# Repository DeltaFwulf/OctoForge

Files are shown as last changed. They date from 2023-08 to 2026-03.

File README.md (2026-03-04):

# OctoForge: 
A work in progress electric furnace capable of reaching chamber temperatures of 1200 C.

This project is simply a display of technical knowledge and something through which we have learned further technologies. The hope is that any projects tackled in the future will be easier due to the experience and skills learned here.

There are three main areas of which the furnace is comprised:
- Mechanical - Frame design complete and in production, insulation under final design iteration, heating element under final design iteration.
- Power electronics - Still iterating over design and testing.
- Control electronics - Yet to be started.

Progress is being tracked [here](https://github.com/users/DeltaFwulf/projects/2).

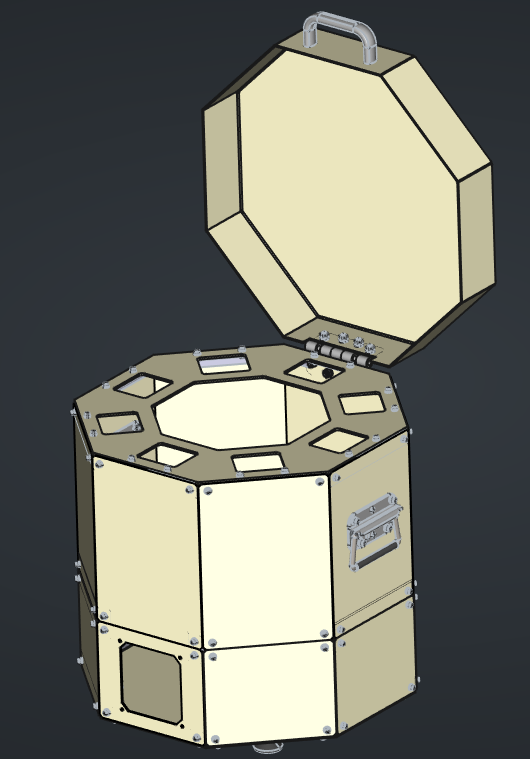
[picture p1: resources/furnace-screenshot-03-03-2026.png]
Screenshot of OctoForge


## How to use this project?
The following software is required to view the various CAD files:
- FreeCAD-1.0.2
- KiCAD-9.0

## How to reproduce OctoForge?
- Sheet metal components were ordered from [Fractory](https://fractory.com/) with the following parameters:
  - Thicknesses:
    - Plates: 3mm
    - Lower panels: 2mm
    - Upper panels: 1.5mm
    - Lid: 2mm
  - High temperature components will be black oxide treated, and exterior components will be painted with high temperature paint and clear coat.
- The other mechanical components were machined from stock using the drawings provided within the CAD directory.
- Fittings were ordered using the provided [BOM](Documentation/Mechanical/BOM.ods) from [Accu](https://www.accu.co.uk/) and [Vital Parts](https://www.vital-parts.co.uk/).
- Feet and handles are standard components, but were sourced from WDS components as listed in the BOM.
- PCBs were ordered from [JLCPCB](jlcpcb.com) with the following parameters:
  - 2 layers
  - PCB thickness - 1.6mm
  - Material type - TG135
  - Outer copper weight - 1oz

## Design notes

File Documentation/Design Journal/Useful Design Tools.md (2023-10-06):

## Product Design Specification

This document outlines the requirements that the design must fulfil, as well as how these requirements were chosen and their priority. This is a very useful tool for constraining the design early on, reducing feature creep and confusion as to where to begin.

## Morphological Charts

This is a graphical method for choosing how to solve different requirements in the PDS. We create a table where the y-axis is requirements and the x-axis consists of concepts of how to solve each requirement. A path is chosen through the table by evaluating the pros and cons of each sub-design concept, allowing a rough image of the overall system to form quickly. Changes can of course be made later on, but this is quite an efficient way to think outside of the one or two examples you thought of on the spot before starting, when a better third option may exist. (brainstorming really helps here)

## Product Breakdown System

This is a super useful way to organise large assemblies. Every component, assembly, and subassembly is assigned a number. This allows easy organisation of parts in spreadsheets containing specific data and CAD structuring through subassemblies. There's a lot more that can be done, such as quantifying progress within a project by assigning weights to not only parts but tasks, and their corresponding progresses.

A good explanation was actually done on Wintergatan's video [here](https://www.youtube.com/watch?v=zVyEsMiwvVc)

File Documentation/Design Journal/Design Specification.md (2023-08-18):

## Product Specification

- Efficient enough to melt copper
- PID control using homemade electronics
- uses standardised components
- relatively portable without causing damage to any party including furnace
- fails safe pls
- easily maintained
- safe power supply: overcurrent protection, requires earthing, hard to shock self on, reasonable safety factor, adequate cooling

## V1 issues
- too easy to touch mains voltage
- hard to control
- ludicrous inefficiency leading to poor performance and high maintenance costs
- difficult to repair
- difficult to manufacture
- choppy voltage source may have led to excessive coil wear
- poor analytical understanding

## Useful links

### References

### Shopping list

## Hardware used

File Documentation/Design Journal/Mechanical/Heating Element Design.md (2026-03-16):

![[heating element model.png]]
*Heating element model*
## Element Geometry
---
Given a maximum power requirement, heating element count, and selected material, the heating element geometry may be defined, and stock sourced.

The general design of a single heating element is that of a coiled wire, bent into a circular loop that sits within a channel on the chamber's inner wall. This element will provide power via radiation into the chamber.

![[steady power vs rockwool thickness, 1200C.png]] 
*Required thermal power required vs rockwool wall thickness.*

Following [[Thermal Modelling]] of furnace insulation, it was determined that the chamber should be able to achieve a temperature of 1200 C for a total power of 154 W. However, if the heating elements provide this steady power, the furnace will take an extremely long time to approach this temperature; more power is required to climb to target temperature than to maintain it.

OctoForge is designed to supply a maximum of 360 W. As such, this value will be used when selecting the elements. As the power board can supply this power evenly between 4 elements, each must supply one quarter of this value, 90 W.

Due to its availability, the first material choice is [Kanthal A1](https://www.kanthal.com/en/products/datasheets/material-datasheets/wire/resistance-heating-wire-and-resistance-wire/kanthal-a-1/). Wire of various diameters may be sourced in coil form, saving production effort.

### Step 1: Calculate Element Resistance
As the power required and chamber temperature are known quantities, the radiative flux may be calculated. Two values are required: the emissivity of the heating element, and the maximum permitted element surface temperature.

Heat flux via radiation between two grey bodies at similar temperatures is given by:
$$q''_{rad} = \epsilon\sigma\left(T_{element}^4 - T_{wall}^4\right)  $$

From Kirchoff's rule, the absorptivity is equal to the emissivity. The heating element and walls are assumed perfect grey bodies. The maximum permitted flux is obtained from [this source](https://www.heating-element-alloy.com/article/heating-element-design-factors.html), set at 50,000 W/m^2. The radiative heating equation may be rearranged for the maximum element temperature, assuming a wall temperature of 1473K.

$$T_{element} =\sqrt[4]{\frac{q''_{max}}{\epsilon\sigma} + T_{wall}^4}$$

Assuming an emissivity of 0.7, the maximum element temperature is calculated to be 1563 K, lower than the maximum allowed temperature of 1673 K for Kanthal A1. To achieve the required 90 W at this temperature, the element would require 0.0018 m^3 of area. This is achieved by a combination of wire diameter and length, however a second constraint exists. The wire must have the correct resistance such that it will dissipate 90 W with a 12 V drop across it.

The resistance of the wire at temperature, $R_t$, may be calculated from the following:
$$ V = IR \xrightarrow{} I = \frac{V}{R}$$
$$Q = VI$$
$$ Q = \frac{V^2}{R} \xrightarrow{}R = \frac{V^2}{Q} $$
This gives a working resistance of 1.6 $\Omega$. 

### Step 2: Calculating Element Length

#### Solving length for total resistance:
The resistance of an element is a function of its resistivity, cross sectional area, and length:

$$ F\rho_0 = R \frac{A_c}{l} = R \frac{\pi D^2}{4l}$$
$$R = \frac{4F\rho_0 l}{\pi D^2}$$
where:
- $\rho$ is the material resistivity at 20 C
- D is the wire circular diameter
- F is the resistivity temperature factor (accounts for higher operating temperatures)

Rearranging for length:
$$ l = \frac{\pi R D^2}{4F\rho_0} $$
#### Solving length for correct flux:

The area of an element may be found, given total power and surface flux:
$$ Q = q''A_s = q''\pi Dl$$
From Ohm's law:
$$ V = IR $$
$$ Q = VI = \frac{V^2}{R} $$

substituting for Q:
$$ q'' \pi Dl = \frac{V^2}{R} $$
Rearranging for l:
$$ l = \frac{V^2}{q''\pi DR} $$
 $$R =FR_0 = \frac{F\rho_0 l}{A_c} = \frac{4F\rho_0l}{\pi D^2}$$
$$ l = \frac{V^2 \pi D^2}{4q'' \pi DF \rho_0 l} $$
Simplifying:
$$ l^2 = \frac{V^2 D}{4q'' F \rho_0} $$
$$ l = \frac{V}{2}\sqrt{\frac{D}{F\rho_0 q''}} $$
Does this also satisfy the relation for resistance?
Setting values for V, D, F, rho, and q, we obtain:
$$ l = \frac{12}{2}\sqrt{\frac{0.001}{1.04*1.45*10^{-6}*50000}} = 0.69098\ m$$
Solving for resistance at this length:
$$ R = \frac{4*1.04*1.45*10^{-6}*0.69098}{\pi 0.001^2} = 1.3267 \ \Omega $$
This doesn't solve the problem with the correct resistance; the solution is incomplete. The value of l is only solved when both relations are satisfied. This requires some extra degree of freedom, as in both equations, the diameter is fixed. This degree of freedom could be the surface flux, recalculating each time for F (this is very insensitive so will be quite well-behaved).

Equating the two lengths:
$$ \frac{\pi RD^2}{4F\rho_0} = \frac{V}{2}\sqrt{\frac{D}{F\rho_0q''}}$$
$$ \frac{\pi^2R^2D^4}{16F^2\rho_0^2} = \frac{V^2D}{4F\rho_0q''}$$
$$ q'' = \frac{V^2 D 16 F^2 \rho_0^2}{\pi^2R^2D^4 4F\rho_0} = 
         \frac{4V^2F\rho_0}{\pi^2 R^2 D^3}$$
Once q'' has been solved, the length can be calculated from either of the two original equations. Note that if the solved surface flux exceeds the maximum chosen value, the total power per element must be reduced (for a given total power, more elements must be used). 

For this element, the total power is given as 90 W. This requires 1.6 Ohms of resistance. The expected surface temperature, from the maximum flux estimate, is 1563K. This gives a resistivity factor of 1.04. Once the flux is calculated, the new element temperature must be solved and F updated.

For a 1mm diameter wire:

| Variable | Value | Unit |
| --- | --- | --- |
| Q | 90 | W |
| V | 12 | V |
| R | 1.6 | $\Omega$ |
| F | 1.04 | ul |
| D | 1.0 | mm |
| $\rho_0$ | 1.45 | $\mu \Omega$ m^2 / m |
| q'' | 34378.27761 | W/m^2 |
| T_new | 1536.52514  | K |
| F_new | 1.04 | ul |
| l | 0.83331 | m |
The following Python function can be used to calculate Kanthal A1 wire length for a given power output and wire diameter:

```python

def wireLength(D:float, Q:float, voltage:float, qMax:float, Tchamber:float):
	"""Calculates the length of Kanthal A-1 wire that satisfies power requirements"""

    # Kanthal A-1 material properties:
    emissivity = 0.7
    resistivity = 1.45e-6
    
    T_el = (qMax / (emissivity*5.67 / 10**8) + Tchamber**4)**0.25
    T_arr = [373, 473, 573, 673, 773, 873, 973, 1073, 1173, 1273, 1373, 1473, 1573, 1673]
    F_arr = [1.00, 1.00, 1.00, 1.00, 1.01, 1.02, 1.02, 1.03, 1.03, 1.04, 1.04, 1.04, 1.04, 1.05]

    F0 = np.interp(T_el, T_arr, F_arr)
    R = voltage**2 / Q
    q = (4*voltage**2*F0*resistivity) / (pi**2 *R**2 *D**3)
    T_el = (q / (emissivity*5.67 / 10**8) + Tchamber**4)**0.25
    F1 = np.interp(T_el, T_arr, F_arr)
    l = pi*R*D**2 / (4*F1*resistivity)

    print(f"Required wire length of Kanthal A-1: {'%.4f' % (l*1000)} mm, at a flux of {q} W/m^2, surface temperature: {T_el} K")
```

### Step 3: Calculate coil and loop geometry

The element is composed of a tight helix, looped into a major circular profile. To avoid excessive self heating of the element, several coil constraints are introduced:
- minimum coil diameter
- minimum pitch

The mean pitch is calculated at the loop mean diameter, referred to here as the pitch diameter, $D_p$.The minimum pitch is set at 3 wire diameters, to mitigate self heating. This is taken at the minor diameter, where the coils are bent closest together. The coil diameter itself should lie between 3 and 6 wire diameters, as per the [design guide](https://www.heating-element-alloy.com/article/heating-element-design-factors.html).

From this, a solution exists with some coil and loop diameter, and some pitch (driven by the loop diameter and wire diameter).

The minimum pitch is set as 3 wire diameters, $p_m = 3d_w$. The loop diameter, D, is chosen to just seat the wire within the chamber wall with no free hanging wire in the chamber, to prevent short circuits and stresses on brittle hot wires.

For a helical wire, the length of the wire along the path is related to the overall coil length by its coil diameter and pitch:

$$ l = \frac{L}{sin(\alpha)} $$
where L is the coil length, l is the wire length, and $\alpha$ is the ramp angle of the helix. This angle can be calculated as:
$$ \alpha = \arctan\left(\frac{p}{\pi d_c}\right) $$
Substituting and rearranging for L:
$$ L = l\sin\left(\arctan\left(\frac{p}{\pi d_c}\right)\right) $$
This helical wire will be bent into a circular arc about its centrum, such that the mean helical pitch is still p.
$$ L = \frac{D\theta}{2} $$
Where D is the loop diameter (through the centre of the coil), and $\theta$ is the angular sweep of the arc. Substituting for L in the previous equation:
$$ \frac{D\theta}{2} = l\sin\left(\arctan\left(\frac{p}{\pi d_c}\right)\right) $$
Rearranging to solve for p:
$$ p = \pi d_c \tan\left(\arcsin\left(\frac{D\theta}{2l}\right)\right)$$
The true constraint is the minimum pitch, $p_m$:
$$ p_m = \left(\frac{D - d_c}{D}\right)p \xrightarrow{} 
   p = \left(\frac{D}{D - d_c}\right)p_m$$
Substituting for p and rearranging for $d_c$:
$$ d_c^2 - Dd_c + \frac{Dp_m}{\pi}\cot\left(\arcsin\left(\frac{D\theta}{2l}\right)\right) = 0 $$
The solution of coil diameter is found by solving the quadratic:
$$ d_c = \frac{D \pm \sqrt{D^2 - \frac{4Dp_m}{\pi}\cot\left(\arcsin\left(\frac{D\theta}{2l}\right)\right)}}{2} $$
The solution chosen is up to the designer, though care must be taken to ensure the loop inner and outer diameters are as expected, or iterate until desired result is achieved.

The chosen wire is AWG 18, or 1.02 mm diameter, made from Kanthal A1. This gives a required length of 866.9796 mm.

Alternatively, since the planned coiling jig (link to this), will use some shaft with a given diameter, the coil diameter becomes a fixed quantity, or at least not the driven value. Instead, the coil diameter should be set based on available coil shaft diameters, and the pitch calculated. From before:

$$ L = l\sin\left(\arctan\left(\frac{p}{\pi d_c}\right)\right) $$
Rearranging for p and substituting for L:

$$ p = \pi d_c\tan\left(\arcsin\left(\frac{D\theta}{2l}\right)\right) $$
And for minimum pitch:
$$ p_m = \pi \frac{d_c(D - d_c)}{D} \tan\left(\arcsin\left(\frac{D\theta}{2l}\right)\right)$$

There exists a window of valid coil diameters, due to the parabolic nature of the minimum pitch equation. Any value of $d_c$within this window may be used to create heating elements. The bounds are given by the solution of the quadratic:

letting k = $\frac{\pi}{D}\tan\left(\arcsin\left(\frac{D\theta}{2l}\right)\right)$:
$$ d_c^2 - Dd_c + \frac{p_m}{k} = 0 $$
$$ d_c = \frac{D \pm \sqrt{D^2 - \frac{4p_m}{k}}}{2} $$

The proposed solution method is as follows:
1. Calculate, given the minimum pitch constraint, a valid coil diameter.
2. Adjust the coil diameter to some useable value and check the minimum pitch.
3. Repeat until a valid coil diameter is found, using the solved pitch.
4. Calculate the stretched loop length from the equation for L.

A short python function to help calculate this geometry has been added below:

``` python
def coilDiameterBounds(dLoop:float, lWire:float, dWire:float, minPitch:float, arcAng:float) -> float:

    """Calculate the minimum and maximum coil inside diameters, then calculates the required coil pitch and stretched length for a valid, chosen coil diameter."""

    try:
        k = pi*tan(asin(0.5*dLoop*arcAng / lWire)) / dLoop
        dcMin = (dLoop - sqrt(dLoop**2 - (4*minPitch / k))) / 2
        dcMax = (dLoop + sqrt(dLoop**2 - (4*minPitch / k))) / 2

    except:

        print("Zero-length window for coil diameter, adjust inputs and try again.")

        return

    print(f"Minimum coil diameter: {'%.1f' % (dcMin*1000)} mm, Maximum coil diameter: {'%.1f' % (dcMax*1000)} mm.")

    print(f"Minimum shaft diameter: {'%.1f' % (1000*(dcMin - dWire))} mm, Maximum Shaft Diameter: {'%.1f' % (1000*(dcMax - dWire))} mm")

    while True:
        try:
            dCoil = float(input("Enter shaft diameter (mm): ")) / 1000 + dWire
        except TypeError:
            print("Only numeric inputs are accepted, please try again.")

        if dCoil >= dcMin and dCoil <= dcMax:
            break
            
        print("Input outside of valid range, try again.")

    meanPitch = pi*dCoil*tan(asin(0.5*dLoop*arcAng / lWire))
    minorPitch = meanPitch*(dLoop - dCoil) / dLoop

    print(f"Mean pitch: {'%.3f' % (1000*meanPitch)} mm, minimum pitch: {'%.3f' % (1000*minorPitch)} mm.")

    print(f"Stretched length: {'%.1f' % (500*dLoop*arcAng)} mm")
    print(f"Minor loop diameter: {'%.1f' % (1000*(dLoop - dCoil - dWire))} mm")
```

| Variable | Value | Unit |
| --- | --- | --- |
| Q | 90 | W |
| V | 12 | V |
| R | 1.6 | $\Omega$ |
| F | 1.04 | ul |
| D | 1.02 | mm |
| $\rho_0$ | 1.45 | $\mu \Omega$ m^2 / m |
| q'' | 32395.419 | W/m^2 |
| T_new | 1533.07 | K |
| F_new | 1.04 | ul |
| l | 866.9796  | mm |
| $p_m$ | 3.06 | mm |
| D | 83 | mm |
| $\theta$ | 300 | deg |
| $d_{shaft}$ | 5 | mm |
| $d_c$ | 6.02 | mm |
| $\bar{p}$ | 4.896 | mm |
| L | 217.3 | mm |
| $D_i$ | 76 | mm |

This coil has a minimum pitch of 4.541 mm. This means that, should the element have to little resistance, it can be compressed by about one third and still meet the minimum pitch constraint.

![[coil geometry.png]]
*Heating element coil model.*

One concern with resistive heating elements is hot-spotting, where thinner sections (with higher resistance) radiate at a higher surface flux than the bulk element. This causes premature burnout of elements and so more maintenance tasks. To mitigate this, a larger wire gauge, 18 AWG, was chosen despite being more expensive than finer wire gauges. For the same area deviation (caused, for example, by scratches, oxidation, etc) the proportional local area change is smaller the larger the nominal area is. In future, thinner elements may be designed following the same method, however they will require more careful handling and inspection prior to use.

To model the heating element in FreeCAD, the *PathHelix* macro was used, from the [GrabBag](https://github.com/pyro9/GrabBag) repository by pyro9. Click [here](https://www.youtube.com/watch?v=COVKF25ttLY) for an installation guide. To create the full path, multiple sketches were [joined](https://www.youtube.com/watch?v=jE-H_30MbcA) together in a single binder, then an additive pipe used to sweep the wire cross section - beware, this takes a VERY long time to render.

Following the advice found in [this](https://www.youtube.com/watch?v=I-5_MN5_Fmc&list=PLhA0ygLQR39mygehFiBQ72nzciFNVJfHL&index=18) video, a coil winding jig was designed to produce these elements from Kanthal wire stock.

![[coil winding jig.png]]
*Coil winding jig model*

The jig will be mounted in a vice with the wire inlet groove accessible. A length of wire is threaded into the block and passed out of the front (wider hole side). This is then passed through the notch on the winding shaft and secured. The shaft is then backed off into the jig block. Next, a drill is attached to the free end of the winding shaft. To wind the coil, the drill is spun while slight compression is applied to the coil to keep the layers in contact.

The coil, once produced in the jig, is stretched to length on the shaft to attain the desired pitch.
## Power Delivery
---
To supply power to the elements, terminals are required. These must withstand the extreme temperatures of the chamber and elements, provide reliable electrical connection, and allow for simple element replacement in the event of damage.

The proposed solution is to use stainless steel threaded bars and nuts to clamp the elements. Two nuts will clamp the elements in the chamber, and two others will clamp a copper wire on the supply side.  The inner nuts will be spaced such that they are located axially in the bricks, and the outer nuts used to clamp the terminals.

The terminals will be made from M4 threaded bar, with two full hexagonal nuts on each end. On the chamber side, the connection will be purely between the nuts, washers, and the wire; the outer connection will use a spade terminal between the nuts.

To minimise heat dissipation along the transmission lines, the resistance must be minimised. Copper wires will be used, with a total transmission resistance << 1$\Omega$.

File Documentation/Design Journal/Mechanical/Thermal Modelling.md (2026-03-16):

## Modelling the chamber as a resistance network

A good method we can use to model the furnace is as a resistance network. Using this we can calculate the heat loss though multiple sides using simple analytical techniques. As a first attempt, the cylinder may be modelled as a cylinder wall with a lid and a floor surrounded on all sides by ambient air subject to convective heat transfer. 

Total resistance for a single wall, $R_{wall}$, is equal to the sum of the inline resistances between the chamber air and the ambient air.

## Parameterising air properties

To save manually looking up values in dry air tables, I will create functions to predict air conductivity and viscosity:

### Assumptions
- air is at 101325 Pa
- mean mass of an "air" molecule to be $0.02896 \div 6.022\ast 10^{23} = 4.809 \ast 10^{-26}$ kg
- air is dry

### Viscosity 
[Source](https://en.wikipedia.org/wiki/Temperature_dependence_of_viscosity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,gaseous%20viscosity%20increases%20with%20temperature) 

$$\mu = \frac{5}{16\sqrt{\pi}} \times \frac{(mk_bT)^\frac{1}{2}}{\sigma\Omega(T)}$$

$$\Omega(T)  = 1.16145T^{\ast-0.14874} + 0.52487e^{-0.77320T^\ast} + 2.16178e^{-2.43787T^\ast}$$

where:

$T^\ast=\frac{k_bT}{\epsilon}$,  
($k_b/\epsilon = \frac{1}{97}$) K$^{-1}$,
$\sigma = 3.617 \ast 10^{-10}$ m

### Thermal conductivity, $\lambda$
Using [this paper](https://srd.nist.gov/jpcrdreprint/1.555749.pdf), I have tied the thermal conductivity of the air to both its temperature and density. This seems to match known values of k through the ranges of temperatures (and pressures) that we require.

$\lambda(\rho,T) = \lambda_0(T) + \lambda_R(\rho)$ W/m$\ast$K

$\lambda_{0R} = \frac{\lambda_0}{\Lambda}$,

$\Lambda = \frac{R^\frac{5}{6}p_c^\frac{2}{3}}{(TMN_A^2)^\frac{1}{6}} = 4.358\ast10^{-3}$ W/m$\ast$K,

$$\lambda_{0R} = C_1T_R^{-1} + C_2T_R^{\frac{-2}{3}} + C_3T_R^{\frac{-1}{3}} + C_4 + C_5T_R^{\frac{1}{3}} + C_6T_R^{\frac{2}{3}} + C_7T_R + C_8T_R^{\frac{4}{3}} + C_9T_R^{\frac{5}{3}}$$

where:
$C_1 = 33.9729025$,
$C_2 = -164.702679$,
$C_3 = 262.108546$,
$C_4 = -21.5346955$,
$C_5 = -443.455815$,
$C_6 = 607.339582$,
$C_7 = -368.790121$,
$C_8 = 111.296674$,
$C_9 = -13.4122465$

Critical values:
$T_c = 132.52$ K
$\rho_c = 313$ kg$\ast$m$^{-3}$

$\Delta\lambda_R = D_1\rho_R + D_2\rho_R^2 + D_3\rho_R^3 + D_4\rho_R^4$

where:
$D_1 = 3.12013125$
$D_2 = -23.0762400$
$D_3 = 1.65049430$
$D_4 = -0.191148175$

How do we iterate to arrive at the correct answer for the cylinder surface temperatures? (calculating the film temperatures?) There seem to be two unknowns (Ts1, Ts2) and one equation

**19/08/2023**
Okay, so the initial question was incomplete. I need to set more design constraints to be able to solve for the wall thickness. I'll set the outside wall temperature to a temperature that's either:

1. safe to touch comfortably - I need to find a temperature chart for this
2. low enough to hold the handles (modelling conduction)
3. some other arbitrary value if we use a shroud like [Here](https://www.hswalsh.com/product/melting-crucible-furnace-3kg-italian-manufactured-tf58b)

I'll also be aiming to minimise the heat loss for a given chamber-ambient temperature difference within some design constraint (I can't just make the walls 10km thick due to cost and maintenance restrictions, never mind portability lol)

I'll define the thermal efficiency of the furnace at temperature T as $1-(\frac{Q_{loss}} {Q_{max}})$ for the time being, and aim for an efficiency greater than 80% at 1000$^{\circ}$C

So, we can solve for wall thickness given a certain heat loss, chamber temperature and wall outer temperature. Therefore we can solve for furnace performance over a range of temperatures (if not efficiently): 
1. solve the specified case to get target wall thickness
2. for each temperature we want to investigate, alter the heat flux and solve for wall thickness as in the specified case; when the wall thickness equals the target wall thickness this is the performance of the furnace at this temperature. We can use a shooting method to obtain results relatively efficiently.

We can predict floor and lid performances similarly, assuming the furnace is airtight

To get better results, we will need to run a thermal simulation of the frame after initial models have been produced in software such as openFoam.

### Setting boundary conditions 

How hot can the outer wall get if not shrouded? [Possible Source](https://ntrs.nasa.gov/api/citations/20100020960/downloads/20100020960.pdf)

For testing, I'll use 44$^{\circ}$C, but I'll figure out the $k{\rho}c$ of ~~fire bricks~~ later on

**20/08/2023**

Okay, so the method for getting the design point performance is actually very convoluted:
1. Set outer wall radius and outer wall temperature
2. Calculate heat flow from outer wall condition
3. Use shooting method to find inner wall temperature
4. using a shooting method, iterate for chamber temperature to satisfy conservation of energy
5. repeat steps 2-4, varying outer radius until the chamber temperature converges to target
6. vary outer wall temperature  and solve for chamber temperature again until heat flow matches target

I'm almost definitely sure that by setting $T_{s,2}$ to enforce target heat flow in step 1 is possible, however the stability of this algorithm would probably go WAY down, so for now I'm going to do it this way as it seems to be able to converge most of the time.

To calculate the performance of this furnace over different chamber temperatures, we can now fix the wall thickness and not enforce a heat flow target, simply converge to the desired chamber temperature and treat heat flow as a target

I found something saying that $k_{wall}$ will be about 0.2-0.4 [Source](http://www.ccewool.com/News/main-difference-between-insulating-fire-brick-and-refractory-brick/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,better%20than%20refractory%20fire%20brick.)
We'll likely use more VITCAS bricks [Source](https://shop.vitcas.com/insulating-fire-bricks-vitcas-grade-30.html)

$R_{conv,2}$ is returning a complex value, one sec
now Ts1 is coming back complex, might be to do with Q? I'll check in the morning, time to snooze

**21/08/2023**
The problem seems to be the conductivity calculation returning negative, everything else seems to be returning normal results (the viscosity equation is p cool)

**21/08/2023**
I was using $T_{crit}$ not $T_R$ in the conductivity calculation. For some reason, the chamber temperature solver goes unstable after a few iterations, I'll see tomorrow if there's an issue in the chamber temp solver and might have to switch to an inherently stable solver (bisection, etc). I'll also sweep through a range of chamber temperatures and see if the line is super shaky

**26/08/2023**
fuck me, there was a g1 where there should have been a g2, so errors weren't being calculated properly, leading to a runaway chamber temperature

Another seemingly big issue is that if Ts2 is assumed constant when varying $r_{outer}$, power constantly increases at the same time as thermal resistance in the wall, leading to runaway chamber temperatures. I will find, for each value of $T_{s,2}$, the outer radius that gives the target chamber temperature using the shooting method:

**Definition of Shooting Method** (I can't remember its real name so I just rederive it every time I need it)

**Assumption:** there is a monotonic correlation between guesses and cost function output. 

1. make two initial guesses, $g_1$, and $g_2$.
2. calculate the cost function output for these errors i.e. the difference in heat output to target (make sure it is positively correlated with guess magnitude or you may have a problem)
3. calculate the new guess by: $g_3 = g_1 + (\frac{e_1}{e_1-e_2}) \ast (g_2 - g_1)$
4. let $g_1 = g_2$ then let $g_2 = g_3$
5. repeat until $e_2 < e_{max}$
6. return $g_2$ and whatever else useful you may have calculated

this works, the last layer is to solve for $T_{s,2}$ that requires a specific wall thickness (brick thickness in this case)

The next steps will be to create a planar wall version to calculate conductive losses and inner wall temps, but they will be called as variant functions (as arguments into the higher function or smth)

I'll solve for the lowest outer wall temps that I can get away with for the time being, which can give answers for all dimensions, then begin modelling the heating element in a similar (but hopefully slightly simpler) way.

As a sanity check, I'll attempt to perform a simulation on the furnace once the chamber has an initial model (this will take ages but should provide a clearer answer)

**Sanity Check**
The heat loss from the wall seems very low. To check if we're WAY off, I'm going to model the furnace as a planar wall and measure the conductive heat loss through it given assumed inner surface temperature and wall thickness.

Cylinder prediction: ($T_{s1} = 1373 K$, $T_{s2} = 373K$) = 200 W
Cylinder prediction: ($T_{s1} = 416 K$, $T_{s2} = 373K$)  = 17 W

Planar wall prediction: ($T_{s1} = 1373 K$, $T_{s2} = 373K$) = 700 W
Planar wall prediction: ($T_{s1} = 416 K$, $T_{s2} = 373K$)  = 30.4 W

It seems that the prediction for inner wall temperature may be too low? Why is the solved value of $T_{s1} << T_{chamber}$?

I'll set $T_{s1}$ to be equal to the chamber temperature of 1100$^{\circ}$C. I believe this is a better (and conservative) approximation as the inside of the furnace will not form a well developed boundary layer as there is no net flow upwards along the chamber wall. This gives an estimated heat loss of 400W through the walls (this makes more sense intuitively).

**08/09/2023 - 09/09/2023**
Today, I implemented a generalised multilayer wall solver for the cylinder. This allows us to experiment with different materials of different thicknesses more easily. Additionally, I tweaked the chamber dimensions to better fit our expected crucible dimensions of **60mm OD and 145mm chamber height**. The lid and base calculations were also tweaked to be both closer to reality as well as more conservative: I extended the radius of both to that of the furnace outer radius as wall loss calculations previously ignored heat lost through the *top and bottom* of the walls. I initially had stability issues with my solver, but adding a relaxation factor of 0.1 solved this issue; there is a discontinuity between different correlations that was throwing off results. To alleviate this in the future, I plan to blend linearly over a short range between regimes.

**Modelling the lid and base**

Under some conditions, the lid or base are too cold for standard correlations to produce accurate results. To remedy this, I have found a lower range Nusselt correlation [here](https://www.researchgate.net/profile/Sn-Sridhara/publication/285992745/figure/tbl1/AS:669300373336093@1536585052777/Correlation-of-Nusselt-number-with-Rayleigh-numbe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). To the reader of this log, [here](https://www.sfu.ca/~mbahrami/ENSC%20388/Notes/Natural%20Convection.pdf) is a basic explanation for natural convection. 

**Multilayer walls**
I have modelled the addition of a rockwool overwrap and MDF casing to see if we can improve our insulation significantly. 

[MDF properties](https://www.makeitfrom.com/material-properties/Medium-Density-Fiberboard-MDF/)
[Rockwool properties](https://www.researchgate.net/figure/Relationship-between-thermal-conductivity-and-temperature-of-rock-wool_tbl1_340083368)

**Effects of adding rockwool insulation**
I found that by adding only 80mm of rockwool around the firebricks and 12mm of MDF as an outer casing, we can reduce our power use from 220W to only 150W at a chamber temperature of 1100℃. This is definitely worth including, as rockwool is easy to form and fairly inexpensive. It will also protect the fragile firebricks from being damaged by collisions with tools or when being handled/moved.

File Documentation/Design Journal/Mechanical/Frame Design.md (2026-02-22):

The furnace frame represents the mechanical structure that houses the chamber and electronics.

**General Requirements**
- The furnace must be able to be carried by two people via handles
- The furnace must be able to be moved while in operation by provision of touch points < 44°C with a chamber temperature of 1200°C
- The furnace must survive a car journey when not in operation
- The furnace should survive tipping over unless containing molten metal
- The frame must not easily slip along the ground
- On a normal surface, the furnace should be adjustable such that it does not rock
- The furnace should not scratch or damage wooden floors
- The frame must be easy to disassemble into individual components via fastener joints, for maintenance or upgrade purposes
- Electronics must be able to run for over 8 hours continuously within the frame without overheating
- The chamber must be accessible without needing any tools, and quickly re-covered to prevent excessive heat loss when removing i.e. crucibles.

The furnace will take on an octagonal prism shape, as with 8 sides a cylinder is approximated (the most thermally efficient profile for wall thickness) within 8.2%, but angles are cut at 45°, keeping machining operations simple. The frame will be held together by bolted connections to allow any part to be interchangeable, in case it is damaged or needs upgrading.

To simplify manufacture and make the frame as cheap as possible, parts are to be made largely from sheet metal, allowing for quick and low-cost laser cut / bend services to be used. Where this is not possible, simple machining operations that can be performed on a mill / lathe must be chosen, such that these parts can be produced by hand.

## Bill of Materials
Parts have sorted into three categories: machined components, that must be produced from some stock, fasteners (such as bolts, nuts, washers), and off-the shelf components, such as handles, feet, etc.
### Fasteners
---

| NAME | STD | QTY | MATERIAL | SUPPLIER | COST | ORDER | STATUS  |
| --- | --- | --- | --- | --- | ---- | --- | --- |
| *M4 flat washer* | DIN 125  | 192 | A2 SS | Accu | 9.60 | QYMLGSMJN | ORDERED |
| *M4x12 Caphead screw* | ISO 4762 | 50  | A2 SS | Accu | 4.50 | QYMLGSMJN | ORDERED |
| *M4x10 Caphead screw* | ISO 4762 | 50  | A2 SS | Accu | 4.50 | QYMLGSMJN | ORDERED |
| *M4 hex nut* | DIN 934  | 96  | A2 SS | Accu | 5.60 | QYMLGSMJN | ORDERED |
| *M6x16 Caphead screw* | ISO 4762 | 6 | A2 SS | Accu | 1.44 | QYMLGSMJN | ORDERED |
| *M6 flat washer* | DIN 1440 | 12  | A2 SS | Accu | 1.44 | QYMLGSMJN | ORDERED |
| *M6 hex nut* | ISO 4032 | 6 | A2 SS | Accu | 1.68 | QYMLGSMJN | ORDERED |
| M3 x 10 M/F standoff  | N/A | 4 | POM / Brass | Accu | 2.84 | QYMLGSMJN | ORDERED |
| M3 x 6 caphead screw  | N/A | 4 | PC | Accu | 1.64 | QYMLGSMJN | ORDERED |

## Production Information
---
[Fractory](https://fractory.com/) offers relatively affordable laser cut / bending options for mild steel or galvanised steel parts.
[Adjustable Feet](https://www.vital-parts.co.uk/weight-rated-tilting-adjustable-feet---wamf040-2523-p.asp)
[Rockwool Insulation](https://shop.vitcas.com/bio-soluble-fibre-blanket-1200-c-25mm.html)
# February 2026 - Frame Redesign
---
During manufacture of the frame, several issues were highlighted with the lower panel mounting solution and the upper panels. These, as well as final design iterations for other components, are discussed below.

## Lower panel mounting solution
---
When the frame structure was changed from using extruded aluminium sections to using angle bar brackets, a design flaw was missed; the lower frame panels cannot all be attached as the brackets do not retain the nuts like the extruded sections do. Therefore, the final panels to be mounted cannot use this nut and bolt connection. Instead, they must use a connection that only requires exterior access, such as a tapped hole and bolt.

**Design Requirements**
- Brackets must adhere to existing component interfaces, avoiding reworking any other components (including bolts).
- The brackets should be made from aluminium to make machining quicker and easier.
- All components must be made from the same piece of stock.
- The brackets must only require external access to mount the final two panels.
- The brackets cannot impede internal access when mounting the other panels to the frame.
- The brackets must be able to be attached after other panels are installed.

To solve this problem, several block brackets have been designed, and will be machined from either aluminium offcuts or square bar stock. 

The final panels to be installed are the front panel, which holds the controller and power delivery boards, and the rear panel, which holds the ATX power supply. These panels are mounted as shown below:

![[lower panel blocks.png]]

The blocks can all be produced from a single length of 20 mm aluminium 6082T6 square bar using a chop saw and mill for hole drilling.

## Upper Panel Redesign
---
The original design of the upper panels has made drilling the upper holes accurately very difficult with available equipment. To address this, the upper section is to be redesigned. The panel design does not need to be adhered to, however all component interfaces must remain the same, and access cannot be lost to internal components, such as the terminal wiring.

### Single Wraparound Panel vs 8 Individual Panels
Two concepts have been imagined; a split panel design which resembles the current design but with flat panels and brackets as seen in the lower frame section, and a wraparound design, with one thin sheet of metal formed into an octagonal shape, with brackets as before and an access hatch for the terminal wiring. These concepts will be investigated for cost and viability, then one selected and pursued.

**Individual Panels Advantages**
- Repair and replacement will be cheaper for individual panels.
- Upgrading panels is simpler as they are flat and fit into a mill.
- Looser tolerances can be accepted as errors will not stack over the whole perimeter.

**Wraparound Design Advantages**
- The number of parts to produce is almost halved over the panel design.
- Access panels can be added, allowing tool-less opening of the upper frame.
- The upper frame will be stronger, as corners are connected. This permits a lighter sub-assembly, reducing risks of injury when handling the furnace, and improving stability.

Given the high cost of the wraparound design, as well as concerns regarding accuracy over 7 successive bends,  I have decided to go with the individual panel concept. Three panel variants must be designed:

- base panel
- lid hinge panel
- lifting handle panel

The panels have been made thinner, at 1.5 mm thick, to save weight, since the 2 mm lower panels are more than rigid enough.

## Lifting Handles
---
During transportation, the furnace will be lifted and carried by a set of handles on the side of the furnace. These handles must support the full weight of the furnace and be cool enough to touch during operation.

A spring loaded, stainless steel [handle](https://protex.com/95-637SS-spring-loaded-handle-stainless-steel-natural) has been selected, made by Protex. This has available CAD and meets all design requirements, while being made from a highly corrosion resistant material (this lets me trust that it will retain its strength after several years in a garage... in Leeds).

## Selecting the Lid Handle
---
Stupidly, I've lost the original lid handle, but have also produced a lid with drilled holes spaced at 100 mm apart. This means that unless I want to drill a really weirdly shaped object, I have to find a handle that's also 100 mm wide (they're not that common). [this](https://uk.rs-online.com/web/p/drawer-handles-cabinet-handles/9174321) handle would do the trick, but it's not stainless like I want, or the colour I'd like.

**16/02/2026**
After looking further, I found [this](https://www.wdscomponents.com/en-gb/100mm-hole-centres-x-m6-silver-bow-handle-oval-profile)) other handle that fits a bit better and isn't very expensive.

**22/02/2026**
By adding a second washer onto the handle, an M6x16mm bolt could be used instead of the M6x14 currently marked. This saves a few quid on fasteners, as all other M6 bolts are M6x16mm.
- TBH, the distance predicted is 15.8mm and the hole seems to have relief beyond the thread; worst case with one washer I'll have to shim the handle or file down the bolt a tiny amount. Let's stick with one washer.

### Other Changes

> - chamber braces have been redesigned for production
> - fasteners have been selected and added to the GA, see [[Learning to Use FreeCAD Effectively]] for details about how BOM was updated.
> - the bill of materials has been updated to track all frame components
> - the furnace colour has been chosen: an off-white as a reference to [Cooker](https://wallaceandgromit.fandom.com/wiki/Cooker) from *A Grand Day Out*
> - Lid handle has been selected and added to the GA

### Finalising the Chamber Braces
---
**22/02/2026**
Originally, the chamber braces were to be manufactured by Fractory, however, the expected cost of 8 mild steel parts from them is about £70, far too high a price to justify for some brackets. Instead, these will be produced at the hackspace from angle stock. This stock should be thin enough for the jig saw to make cuts through, and not hardened so that any end mill / drill can finish the job on the mill.

**Potential Options**
- Using thin stock, cut blanks, bend to shape with some jig / bender and then drill holes
- Cut the stock on a band saw, or buy from a shop that can cut lengths
- Use a jig saw to cut the stock and clean up rough cuts on the mill
- Order parts pre-made from Fractory or similar

From these four options, the best seems to be to buy the stock online but already cut to length. The brace's width does not need to be very accurate; the important dimension is the hole spacing. By drilling the holes on the mill, this is not a problem. The stock can be obtained for less than £15 and milled for free* (my time is worthless).

The braces will be made from 25 x 25 x 3 mm mild steel, which will be black oxide treated after machining for extra corrosion resistance in the high temperature environment of the chamber (expected in the 200 to 400 degree Celsius range during operation).

## Preventing the furnace from *rusting*

**22/02/2026**
As the furnace is largely manufactured from various grades of mild steel, and given that it will likely be stored in a dank garage for months at a time, rust is an existential concern for OctoForge.

To prevent this, all outer panels will be coated in a pleasing and heat resistant paint. Internal components expecting high heat will be black oxide treated, and where touching aluminium parts, painted or clear coated (if this doesn't already solve the galvanic corrosion issue).

## Further Cost Saving Measures
On Fractory, the cost of adding the two lower panels threatens to add a further £120 to the order cost! To get around this, I can attempt to mill out the front and PSU panel pockets at the hackspace. This would save a lot of money and should be relatively simple to do, by salvaging the upper panel stock now not being used.

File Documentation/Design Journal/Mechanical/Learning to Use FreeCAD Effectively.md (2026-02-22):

# Creating Assemblies
There seem to be two main addons capable of handling assemblies: A2Plus and Assembly4. Each has their own advantages and trade-offs, which will be discussed here.

## 1. A2Plus

**Pros** 
- uses an intuitive constraint system, quick to whip up a small assembly

**Cons**
- document linking seems fairly primitive: only geometry is imported from parts
- no obvious way to integrate subassemblies into parent assemblies
- unclear how to recompute assembly if a component changes

## 2. Assembly 4 (preferred)

**Pros**
- can handle subassemblies
- robust constraints that rely on geometry
- components are automatically recomputed
- actively being maintained, compatible with v0.21

**Cons**
- setting up geometry for EVERY link can be very clunky
- a strict hierarchy is enforced i.e. I can only attach a part to the highest level of subassembly within a parent assembly, not that subassembly's individual components. This leads to excess geometry needing to be defined, or potentially weird subassembly hierarchies. **EDIT** - you can use "import datum object" to pull lower level geometry up to the required level, solving this issue.

For now, I think I'll stick with Assembly 4 as it appears to scale better than A2Plus. With large assemblies coming down the line in future projects, it makes more sense to prepare by learning best practices now.

N.B. it is quite convenient to create simpler assemblies (2 or 3 minor components) just using the Part object with several bodies contained within.

**22/02/2026**
Until further notice, all assemblies must use the integrated assembly workbench for compatibility with existing models.

-------------------------------------------------------------------------------
## Creating part variants

To create multiple variants of a part (for example, side panels with different holes cut into them), it's useful to create a base part, then reference this geometry in different, dependent bodies. To do this, create the base body, create the dependent body, then in the properties tab of the dependent part, select the base body in the base feature row.

**22/02/2026**
A better method for this is to use [clones](https://wiki.freecad.org/PartDesign_Clone). For example, when panels with the same overall footprint but different hole patterns are required, the base panel with only share features should be made in one body, then cloned to create other bodies. These then reference the original geometry directly, and can have their own downstream geometries. [Here](https://www.youtube.com/watch?v=6_FBijwp-l0) is a good video explaining this feature.

-------------------------------------------------------------------------------
## Spreadsheets & Master Documents

note to self: you can use a single spreadsheet in a single master document over multiple directories. I have been working with a single master in each directory, which works until a dimension is shared between subassemblies.

-------------------------------------------------------------------------------
### Creating a Shell

This is called Part Thickness and can be found in the *Part* workbench.
[guide](https://forum.freecad.org/viewtopic.php?f=3&t=3766&p=29741&hilit=enclosure#p29547)

## Generating a Bill of Materials (BOM)
---
**21/02/2026**
Get ready for some bullshit. This is the current best way I've found to add many components to an assembly and also get some sort of information about quantities inside of a BOM. 

- Do not use Draft WB arrays - they will not appear in the assembly BOM [see here](https://github.com/FreeCAD/FreeCAD/issues/26221), and the fastener BOM lists them but gives quantity 0.
- If link arrays are used, they do not appear at all in the BOM, however they do appear in the fastener WB BOM.

To get the fastener BOM to show all fasteners, fasteners can be created, placed using the assembly, but placing the fasteners into their own part containers. To include the fasteners in the assembly, they can later be added by dragging into the assembly and dragging back out (this is the only way the insert component will recognise it as able to be added).

Hot tip: if fasteners are not visible, they are not added to the fastener BOM - use this to hide any duplicates, either those in the assembly or those in the part containers.

Each type of fastener has been added to a part. For example, the lower panel bracket fasteners have all been added to the *Lower panel bracket fasteners* part. In this method, if link arrays are convenient, they have been used; otherwise, placement was manual for each occurrence of each fastener.

The fastener BOM should now show all occurrences of all fasteners this way.

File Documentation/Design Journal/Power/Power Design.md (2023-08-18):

# Objective:
Design a power supply capable of delivering required power for the furnace

## Sub-tasks
- specify a maximum utilisation of coil power at tMax (0->1)
- design power supply capable of delivering wire's maximum power x safety factor
- design coil connector system for ease of replacement / installation (plug + play)

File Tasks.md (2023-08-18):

1. Perform a basic thermal analysis to find the minimum wall thickness for a given power to provide a max chamber temperature
2. Calculate the length of coil required and mounting designs that work for this arrangement and power supply
3.1 Model the furnace chamber
3.2 begin electronics design (PSU, controller)
4. purchase components and tweak chamber design to fit
5. purchase and test electronics, refine
6. write controller code
7. design tooling for manufacturing furnace
8. meet up in garage and start manufacturing components

1.

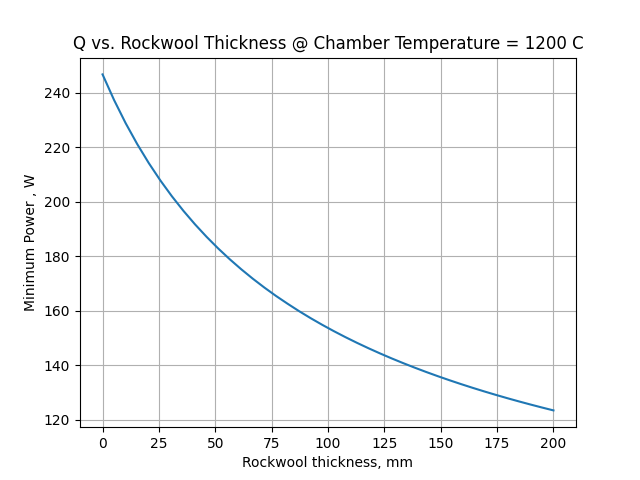
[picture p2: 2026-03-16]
Documentation/Design Journal/Mechanical/Pictures/Steady State Thermal Plots/steady power vs rockwool thickness, 1200C.png

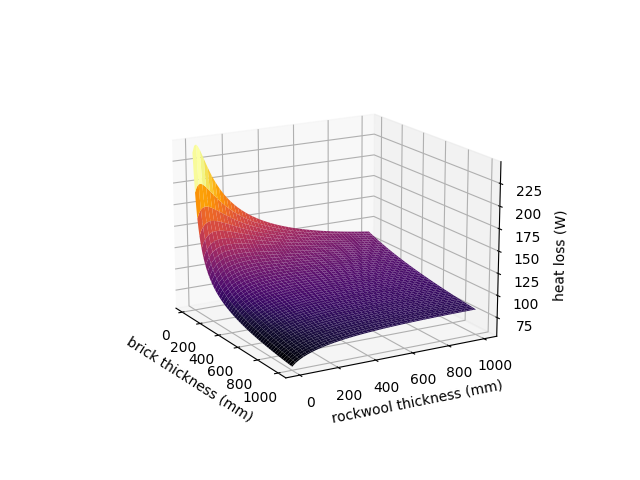
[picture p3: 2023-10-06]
Documentation/Design Journal/Mechanical/Pictures/Steady State Thermal Plots/heat loss against both brick thickness and rockwool thickness.png

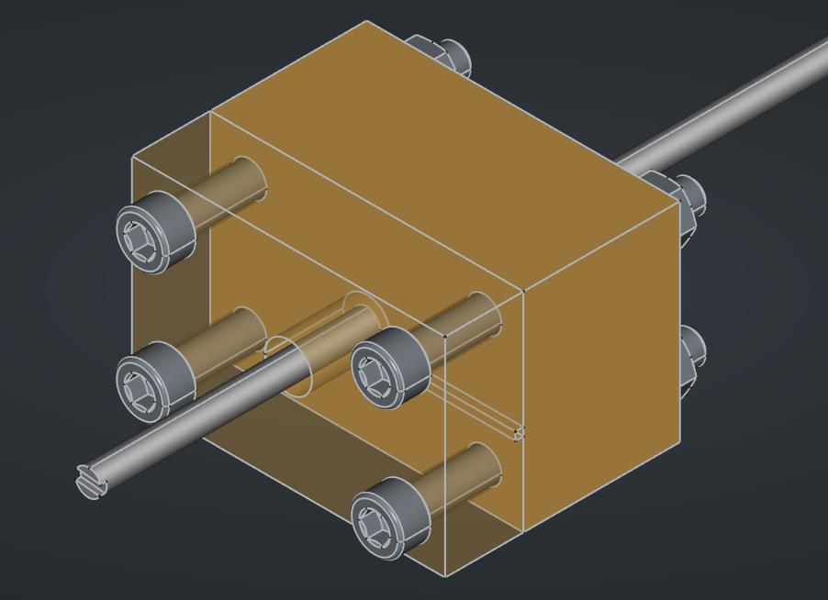
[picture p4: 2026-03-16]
Documentation/Design Journal/Mechanical/Pictures/coil winding jig.png

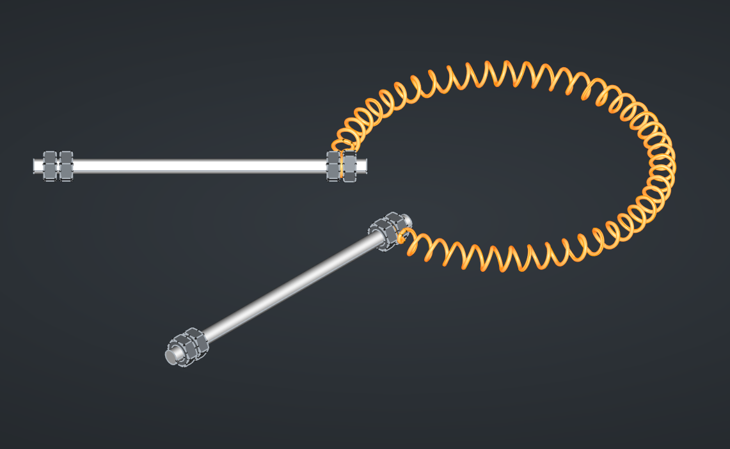
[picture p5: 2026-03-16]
Documentation/Design Journal/Mechanical/Pictures/heating element model.png

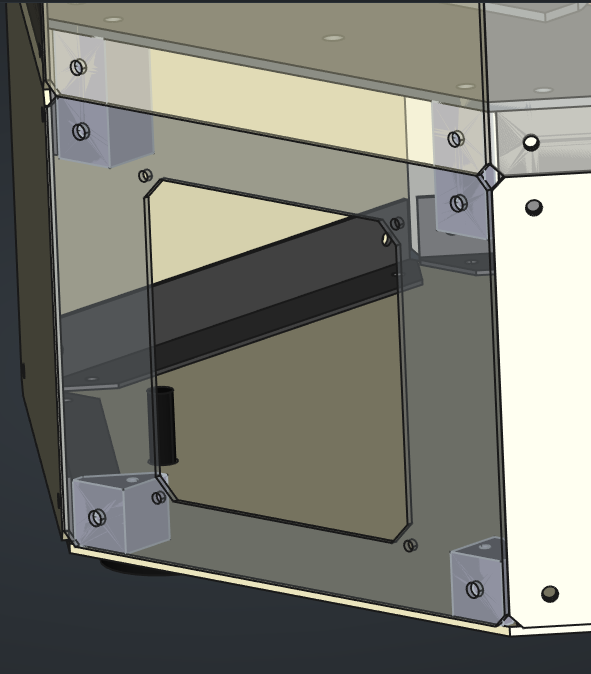
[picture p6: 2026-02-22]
Documentation/Design Journal/Mechanical/Pictures/lower panel blocks.png

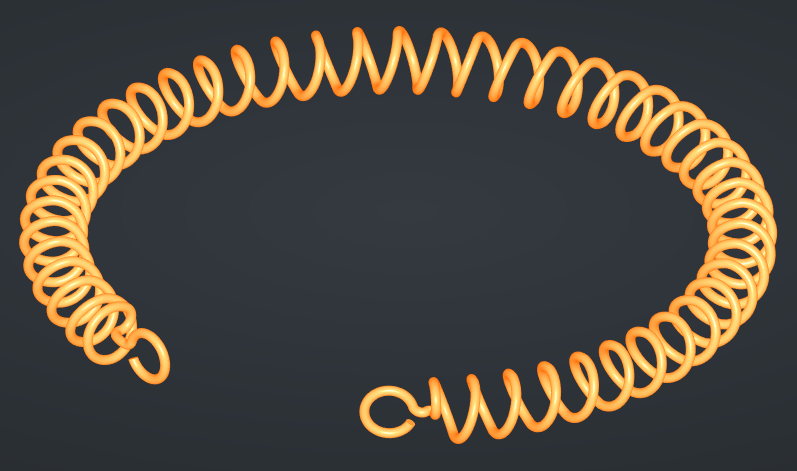
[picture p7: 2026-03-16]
Documentation/Design Journal/Mechanical/Pictures/coil geometry.png

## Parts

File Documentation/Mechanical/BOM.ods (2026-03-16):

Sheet: Frame
Index | Name | Description | File Name | QTY | COTS | Produced By | STOCK / BUY LINK | Design Status | Production Status | Notes
1 | OCT-LIDFR-AA | Lid Frame | ../Design/Mechanical/Frame/mechanical RAD/OCT-LIDFR-AA.FCStd | 1 | FALSE | Fractory |  | COMPLETE | IN PRODUCTION | needs painting
4 | WDS4213-601 | Lifting Handle | ../Design/Mechanical/Frame/mechanical COTS/WDS4213-601.FCStd | 2 | TRUE | N/A | https://www.wdscomponents.com/en-gb/case-fitting-handle-spring-return-stainless-steel | SELECTED | COMPLETE
5 | 637DSS | Lifting Handle Backplate | ../Design/Mechanical/Frame/mechanical COTS/Protex 637DSS Handle Backing Plate Stainless Steel (Natural).FCStd | 2 | TRUE | N/A | https://protex.com/637DSS-handle-backing-plate-stainless-steel-natural | SELECTED | SUPRESSED | Keep in CAD, plan to mill from UFPNL old stock, if unnecessary then cancel
7 | WDS8520-251 | Lid Handle | ../Design/Mechanical/Frame/mechanical COTS/WDS8520-251.FCStd | 1 | TRUE | N/A | https://www.wdscomponents.com/en-gb/100mm-hole-centres-x-m6-silver-bow-handle-oval-profile | SELECTED | COMPLETE
8 | OCT-CHBRA-AC | Chamber Brace | ../Design/Mechanical/Frame/mechanical RAD/OCT-CHBRA-AB.FCStd | 8 | FALSE | Hackspace | https://www.metalsupermarkets.co.uk/product/mild-steel-angle-black-s235-s275/ | COMPLETE | IN PRODUCTION
9 | OCT-LFPNL-BA | Lower Frame Panel, Front | ../Design/Mechanical/Frame/mechanical RAD/OCT-LFPNL.FCStd | 1 | FALSE | Fractory |  | COMPLETE | ORDERED
10 | OCT-LFPNL-AB | Lower Frame Panel, Base | ../Design/Mechanical/Frame/mechanical RAD/OCT-LFPNL.FCStd | 6 | FALSE | Hackspace |  | COMPLETE | IN PRODUCTION | needs painting
11 | OCT-LFPNL-CA | Lower Frame Panel, PSU | ../Design/Mechanical/Frame/mechanical RAD/OCT-LFPNL.FCStd | 1 | FALSE | Fractory |  | COMPLETE | ORDERED
12 | OCT-UFPNL-AB | Upper Frame Panel, Base | ../Design/Mechanical/Frame/mechanical RAD/OCT-UFPNL.FCStd | 5 | FALSE | Fractory |  | COMPLETE | ORDERED
13 | OCT-UFPNL-CB | Upper Frame Panel, Handle | ../Design/Mechanical/Frame/mechanical RAD/OCT-UFPNL.FCStd | 2 | FALSE | Fractory |  | COMPLETE | ORDERED
14 | OCT-UFPNL-BB | Upper Frame Panel, Hinge | ../Design/Mechanical/Frame/mechanical RAD/OCT-UFPNL.FCStd | 1 | FALSE | Fractory |  | COMPLETE | ORDERED
15 | OCT-CPBRC-AA | Top Plate Bracket, Base | ../Design/Mechanical/Frame/mechanical RAD/OCT-CPBRC.FCStd | 7 | FALSE | Hackspace |  | COMPLETE | NOT STARTED
16 | OCT-CPBRC-BA | Top Plate Bracket, Rear | ../Design/Mechanical/Frame/mechanical RAD/OCT-CPBRC.FCStd | 1 | FALSE | Hackspace |  | COMPLETE | NOT STARTED
17 | OCT-LBRAC-AA | Lower Panel, Lower Bracket | ../Design/Mechanical/Frame/mechanical RAD/OCT-LBRAC-AA.FCStd | 6 | FALSE | Hackspace |  | COMPLETE | COMPLETE
18 | OCT-LBLOK-AB | Lower Block | ../Design/Mechanical/Frame/mechanical RAD/OCT-LBLOK-AB.FCStd | 4 | FALSE | Hackspace | https://www.aluminiumwarehouse.co.uk/products/20-mm-x-20-mm-aluminium-square-bar?variant=42544620273852 | COMPLETE | NOT STARTED | missing stock
19 | OCT-UBRAC-AA | Lower Panel, Upper Bracket | ../Design/Mechanical/Frame/mechanical RAD/OCT-UBRAC-AA.FCStd | 6 | FALSE | Hackspace |  | COMPLETE | COMPLETE
20 | OCT-ULBLK-AB | Upper Block, Left | ../Design/Mechanical/Frame/mechanical RAD/OCT-ULBLK-AB.FCStd | 2 | FALSE | Hackspace | https://www.aluminiumwarehouse.co.uk/products/20-mm-x-20-mm-aluminium-square-bar?variant=42544620273852 | COMPLETE | NOT STARTED | missing stock
21 | OCT-URBLK-AB | Upper Block, Right | ../Design/Mechanical/Frame/mechanical RAD/OCT-URBLK-AB.FCStd | 2 | FALSE | Hackspace | https://www.aluminiumwarehouse.co.uk/products/20-mm-x-20-mm-aluminium-square-bar?variant=42544620273852 | COMPLETE | NOT STARTED | missing stock
22 | OCT-LDHNG-AA | Lid Hinge | ../Design/Mechanical/Frame/Mechanical COTS/OCT-LDHNG-AA.FCStd | 1 | TRUE | N/A |  | SELECTED | COMPLETE
23 | WDS673-82225 | Frame foot | ../Design/Mechanical/Frame/mechanical COTS/WDS673-82225.FCStd | 4 | TRUE | N/A | https://www.wdscomponents.com/en-gb/m8-x-25-x-40mm-base-steel-zinc-plated-levelling-foot-tilting-base | SELECTED | COMPLETE
24 | OCT-FRPLB-AA | Base Plate | ../Design/Mechanical/Frame/mechanical RAD/OCT-FRPLB-AA.FCStd | 1 | FALSE | Fractory |  | COMPLETE | IN PRODUCTION | needs painting
25 | OCT-FRPLC-AA | Mid Plate (chamber base) | ../Design/Mechanical/Frame/mechanical RAD/OCT-FRPLC-AA.FCStd | 1 | FALSE | Fractory |  | COMPLETE | IN PRODUCTION | needs painting
26 | OCT-CHTOP-AA | Top Plate | ../Design/Mechanical/Frame/mechanical RAD/OCT-CHTOP-AA.FCStd | 1 | FALSE | Fractory |  | COMPLETE | IN PRODUCTION | needs painting
 | ISO4032 Nut M4 |  |  | 92 | TRUE | N/A | https://www.accu.co.uk/hexagon-nuts/7890-HPN-M4-A2 | SELECTED | COMPLETE | ORDERED on vital parts, quite cheap for fasteners
 | ISO4032 Nut M5 |  |  | 8 | TRUE | N/A | https://www.accu.co.uk/hexagon-nuts/7891-HPN-M5-A2 | SELECTED | COMPLETE | Order 8
 | ISO4032 Nut M6 |  |  | 24 | TRUE | N/A | https://www.accu.co.uk/hexagon-nuts/7892-HPN-M6-A2 | SELECTED | COMPLETE | Order 18
 | ISO4032 Nut M8 |  |  | 4 | TRUE | N/A | https://www.accu.co.uk/hexagon-nuts/7894-HPN-M8-A2 | SELECTED | COMPLETE | Order 4
 | ISO4762 Screw M4x10 |  |  | 64 | TRUE | N/A | https://www.accu.co.uk/metric-cap-head-screws/3838-SSCF-M4-10-A2 | SELECTED | COMPLETE | Order 14
 | ISO4762 Screw M4x12 |  |  | 48 | TRUE | N/A | https://www.accu.co.uk/metric-cap-head-screws/3839-SSCF-M4-12-A2 | SELECTED | COMPLETE
 | ISO4762 Screw M5x14 |  |  | 8 | TRUE | N/A | https://www.accu.co.uk/metric-cap-head-screws/3851-SSCF-M5-14-A2 | SELECTED | COMPLETE | Order 8
 | ISO4762 Screw M6x16 |  |  | 26 | TRUE | N/A | https://www.accu.co.uk/metric-cap-head-screws/3867-SSCF-M6-16-A2 | SELECTED | COMPLETE | Order 20
 | ISO7089 Washer M4 | Actually 0.9mm thick |  | 204 | TRUE | N/A | https://www.accu.co.uk/metric-flat-washers/72488-HPW-M4-A2 | SELECTED | COMPLETE | Order 12
 | ISO7089 Washer M5 | Actually 1.1mm thick |  | 16 | TRUE | N/A | https://www.accu.co.uk/metric-flat-washers/72492-HPW-M5-A2 | SELECTED | COMPLETE | Order 16
 | ISO7089 Washer M6 | Actually 1.8mm thick |  | 50 | TRUE | N/A | https://www.accu.co.uk/metric-flat-washers/72494-HPW-M6-A2 | SELECTED | COMPLETE | Order 38
 | ISO7089 Washer M8 | Actually 1.8mm thick |  | 8 | TRUE | N/A | https://www.accu.co.uk/metric-flat-washers/72496-HPW-M8-A2 | SELECTED | COMPLETE | Order 8

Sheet: Coil Winder
Index | Name | Revision | Description | File Name | QTY | COTS | Produced By | STOCK / BUY LINK | Design Status | Production Status | Notes
1 | OCT-CWRBL | AA | Rear jig block | ../Design/Mechanical/CAD/Tooling/Coil Winder.FCStd | 1 | FALSE | Hackspace |  | COMPLETE | NOT STARTED | Attempt to find some scrap wood for this
2 | OCT-CWFBL | AA | Front jig block | ../Design/Mechanical/CAD/Tooling/Coil Winder.FCStd | 1 | FALSE | Hackspace |  | COMPLETE | NOT STARTED | Attempt to find some scrap wood for this
3 | OCT-CWSFT | AA | Coil winding shaft | ../Design/Mechanical/CAD/Tooling/Coil Winder.FCStd | 1 | FALSE | Hackspace | https://www.metals4u.co.uk/materials/mild-steel/mild-steel-silver-steel/54864-p | IN DESIGN | NOT STARTED
4 | ISO4762 Screw M6x55 | N/A |  |  | 4 | TRUE | N/A | https://www.accu.co.uk/metric-cap-head-screws/3877-SSCF-M6-55-A2 | SELECTED | NOT STARTED | Try to find suitable fastener in the hackspace
5 | ISO4032 Nut M6 | N/A |  |  | 4 | TRUE | N/A | https://www.accu.co.uk/hexagon-nuts/7892-HPN-M6-A2 | SELECTED | NOT STARTED | Use some from existing frame fastener stock

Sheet: Heating Element
Index | Name | Revision | Description | File Name | QTY | COTS | Produced By | STOCK / BUY LINK | Design Status | Production Status | Notes
1 | OCT-HWIRE | AA | Element coil | ../Design/Mechanical/CAD/Electronics/OCT-HELEM-A.FCStd | 4 | FALSE | Hackspace | https://www.ebay.co.uk/itm/174825780935?_skw=Kanthal+A1+iwre&itmmeta=01KJWK9ZWCW11KBBZBM513Y3JX | COMPLETE | NOT STARTED | Blocked by jig production
2 | OCT-PWBAR | AA | Power transmission bar | ../Design/Mechanical/CAD/Electronics/OCT-HELEM-A.FCStd | 8 | FALSE | Hackspace |  | COMPLETE | IN PRODUCTION | Stock received; needs cutting to length.
3 | ISO4032 Nut M4 |  |  |  | 32 | TRUE | N/A | https://www.accu.co.uk/hexagon-nuts/7890-HPN-M4-A2 | SELECTED | NOT STARTED

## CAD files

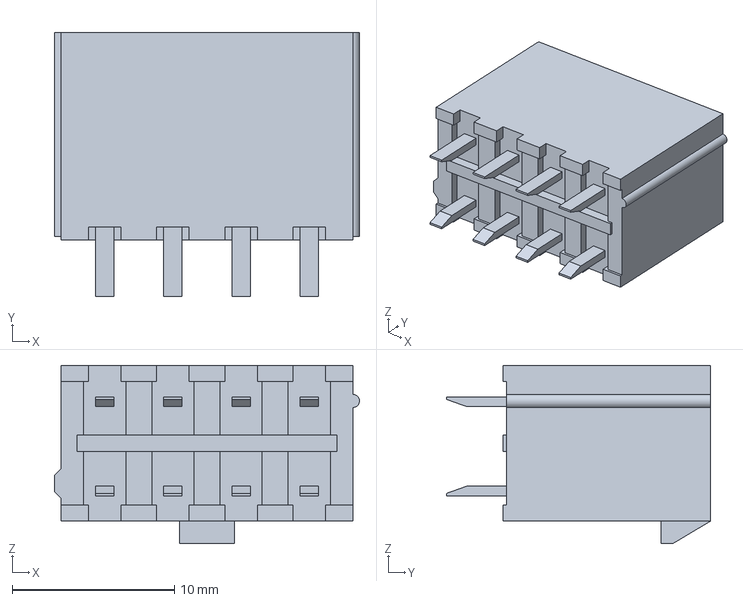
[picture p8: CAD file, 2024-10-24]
Design/Electronic/Power/Resources/3dModels/Molex-Mini-Fit-Jr-5566-8.stp
18.8 x 16.3 x 11.0 mm

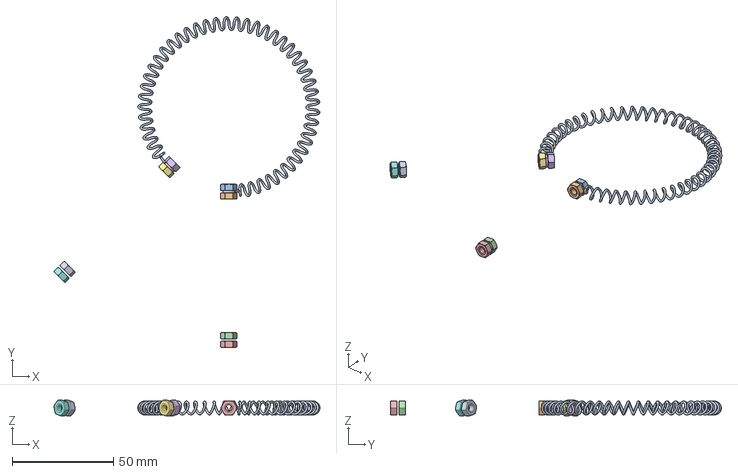
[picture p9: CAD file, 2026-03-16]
Design/Mechanical/CAD/Electronics/OCT-HELEM-A.FCStd
131.3 x 163.4 x 7.81 mm
element body
M4-Nut x 16

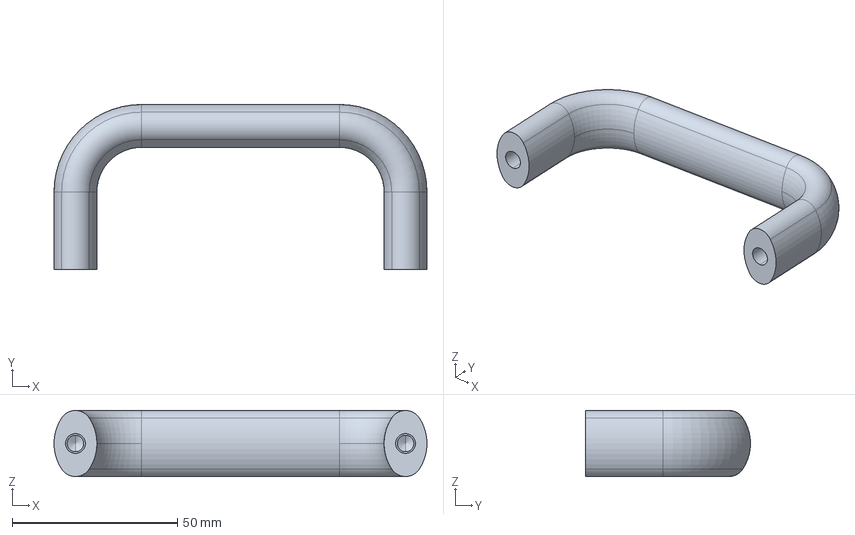
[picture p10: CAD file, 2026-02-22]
Design/Mechanical/CAD/Frame/mechanical COTS/WDS8520-251.FCStd
113.0 x 50.0 x 20.0 mm

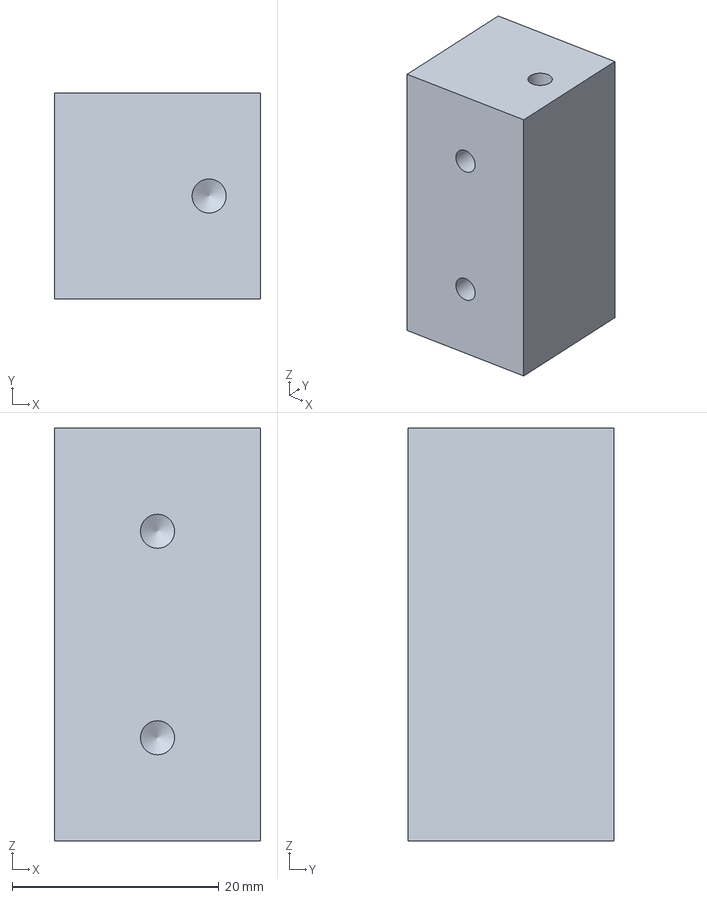
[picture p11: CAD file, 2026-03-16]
Design/Mechanical/CAD/Frame/mechanical RAD/OCT-ULBLK-AB.FCStd
20.0 x 20.0 x 40.0 mm

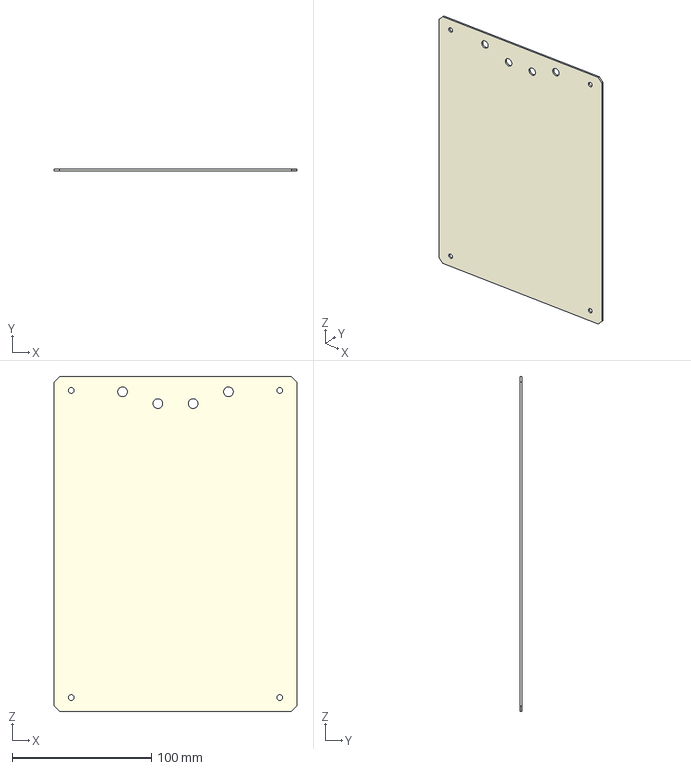
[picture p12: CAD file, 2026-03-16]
Design/Mechanical/CAD/Frame/mechanical RAD/STEP export/OCT-UFPNL-BB.step
174.8 x 1.50 x 241.0 mm

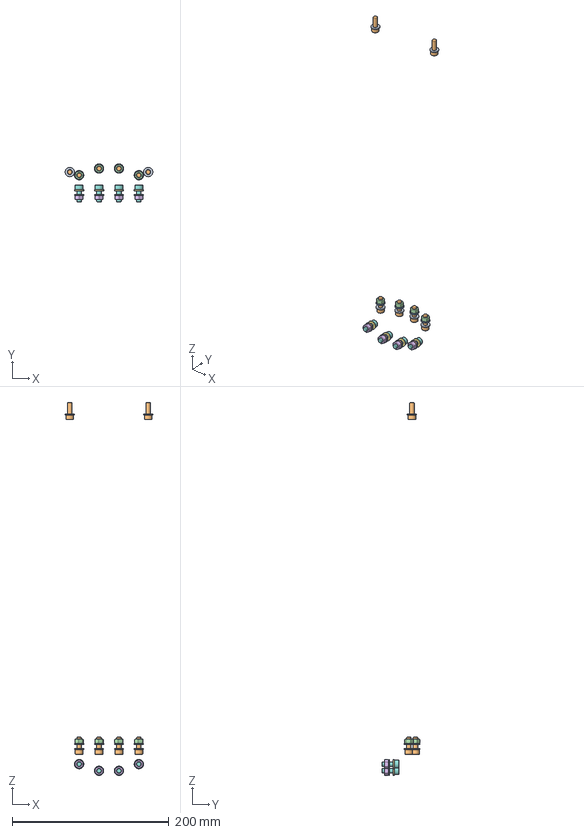
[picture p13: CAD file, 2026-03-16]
Design/Mechanical/CAD/Frame/OCT-FRAME-A.FCStd
112.0 x 48.9 x 475.9 mm
M6-Washer x 36
M6x16-Screw x 20
M6-Nut x 16

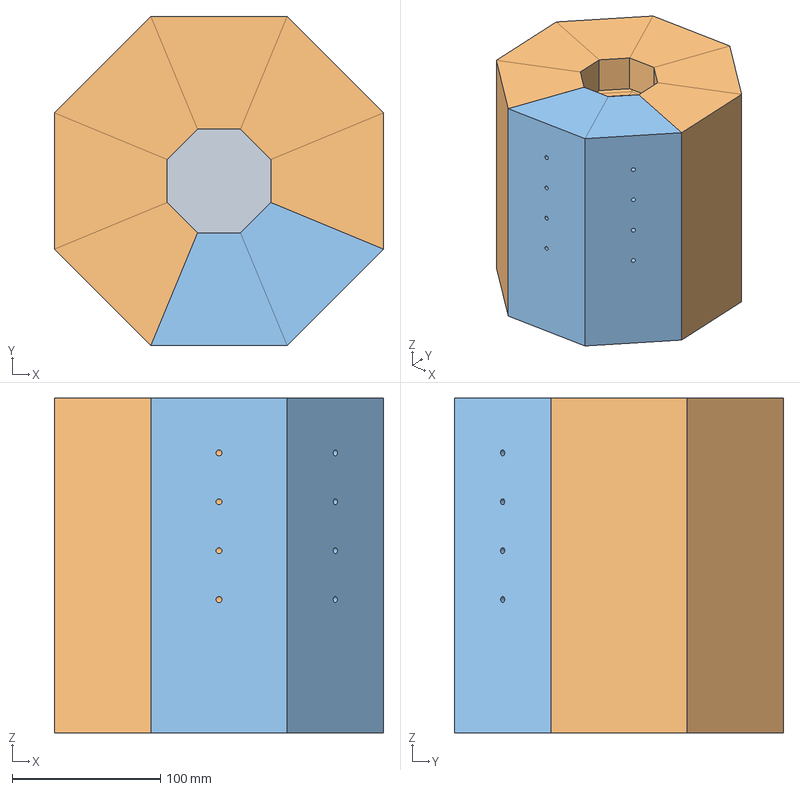
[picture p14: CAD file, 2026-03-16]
Design/Mechanical/CAD/Insulation/OCT-CHMBR-A.FCStd
222.0 x 222.0 x 226.0 mm
OCT-CHBRK-CA
OCT-CHBRK-AA x 6
OCT-CHBRK-BA x 2

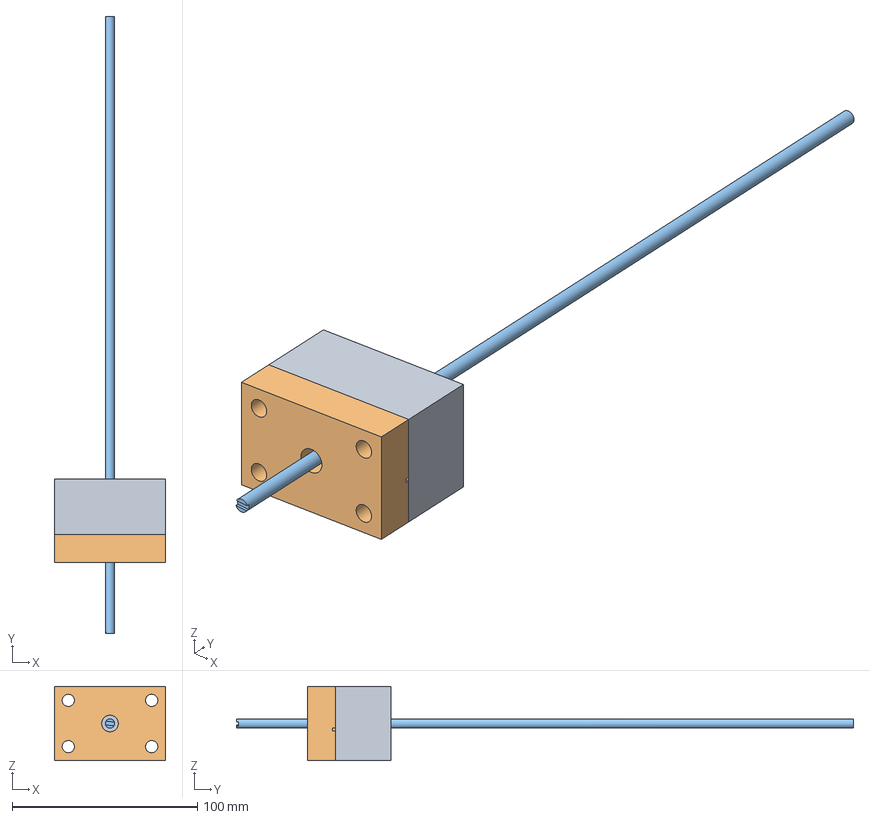
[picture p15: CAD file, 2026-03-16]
Design/Mechanical/CAD/Tooling/Coil Winder.FCStd
60.0 x 333.0 x 40.0 mm
OCT-CWRBL-AA
OCT-CWFBL-AA
OCT-CWSFT-AA

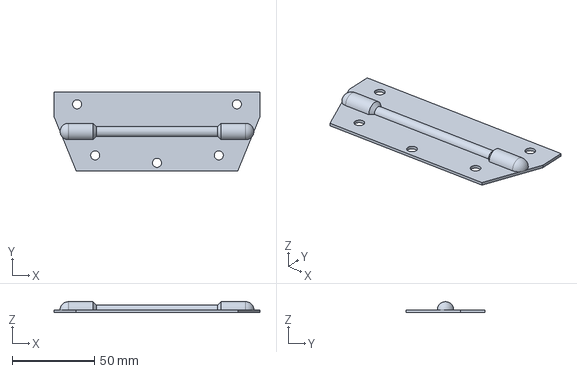
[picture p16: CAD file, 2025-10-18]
Design/Mechanical/mechanical COTS/OCT-CHAND-AA.FCStd
125.0 x 48.0 x 6.50 mm

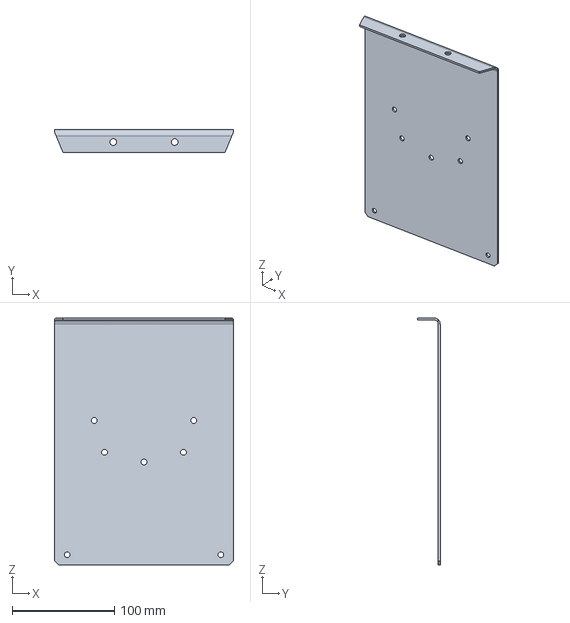
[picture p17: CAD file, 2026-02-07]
Design/Mechanical/mechanical RAD/OCT-UFPNL-CA.FCStd
174.8 x 22.0 x 241.0 mm

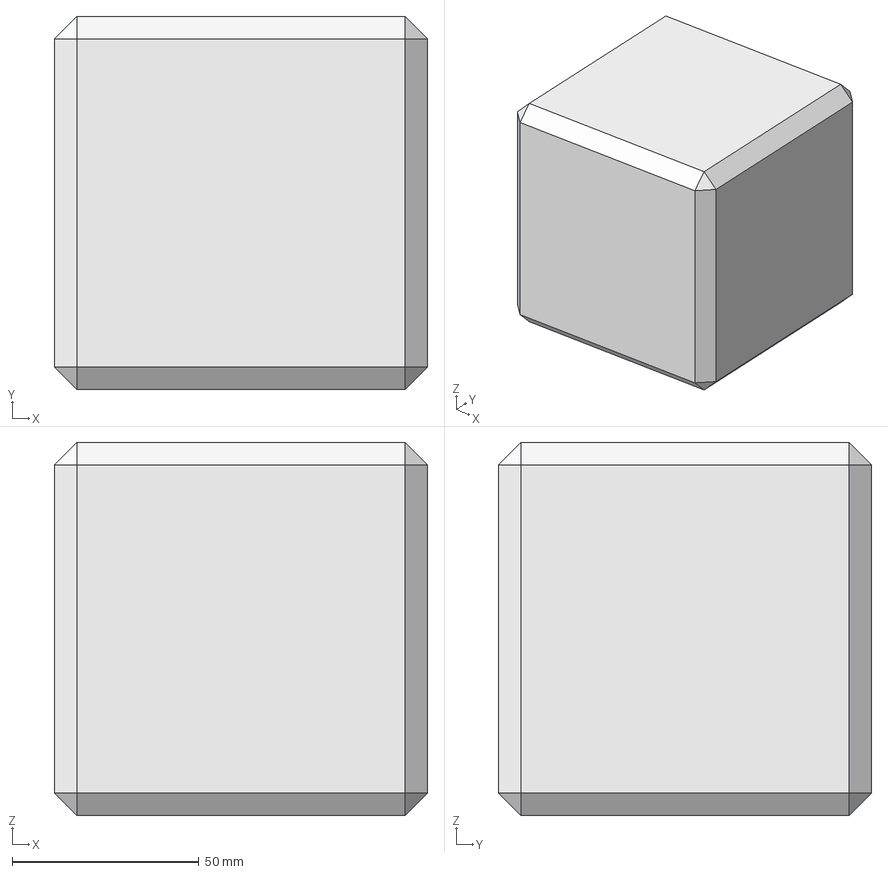
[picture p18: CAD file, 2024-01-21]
Mechanical Design/CAD/link test.FCStd
100.0 x 100.0 x 100.0 mm

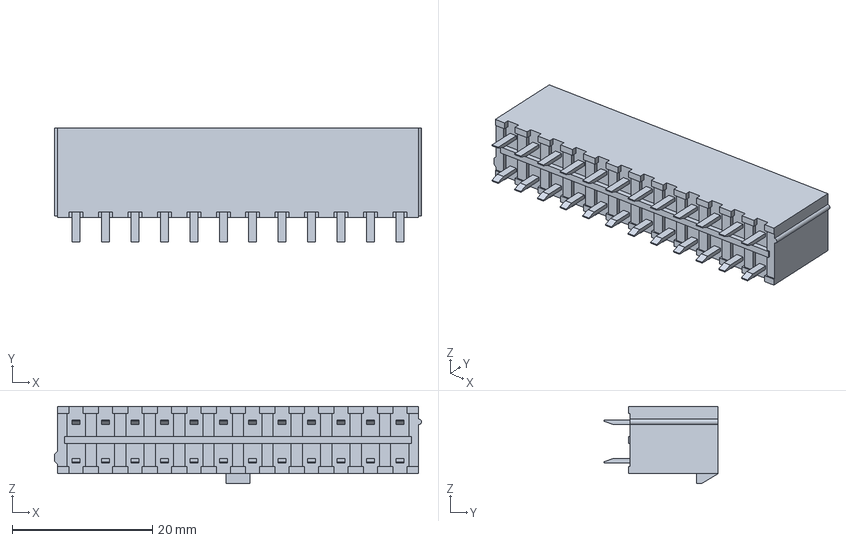
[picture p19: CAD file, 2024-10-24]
Design/Electronic/Power/Resources/3dModels/Molex-Mini-Fit-Jr-5566-24.stp
52.4 x 16.3 x 11.0 mm

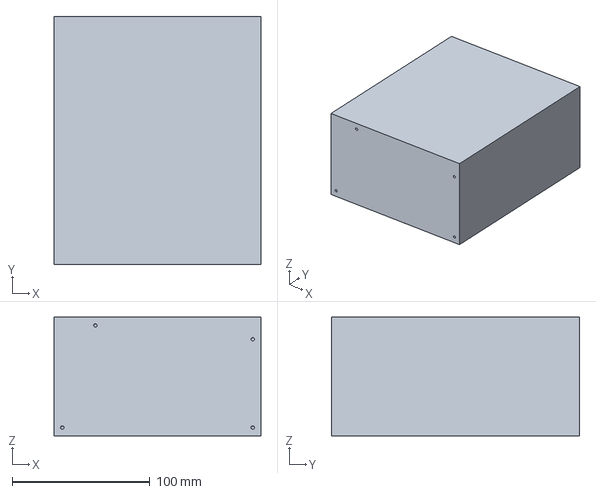
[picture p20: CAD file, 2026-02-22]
Design/Mechanical/CAD/Electronics/OCT-ATXPS-AA.FCStd
150.0 x 180.0 x 86.0 mm

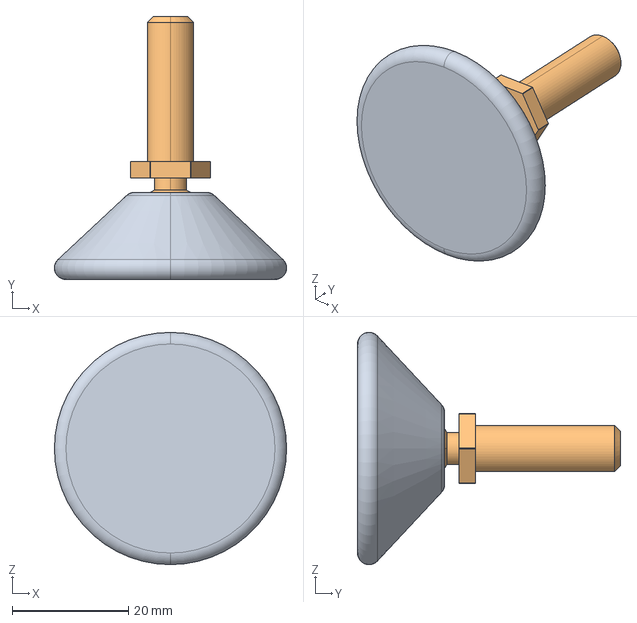
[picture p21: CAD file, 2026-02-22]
Design/Mechanical/CAD/Frame/mechanical COTS/WDS673-82225.FCStd
40.0 x 45.3 x 40.0 mm
WDS673-82225-P7_673-82212-pad
WDS673-82225-P9_673-80225-stem

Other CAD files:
Design/Mechanical/furnace assembly.FCStd
Design/Mechanics/Insulation/chamber subassembly.FCStd
Design/Mechanical/CAD/OctoForge-A.FCStd
Design/Mechanical/CAD/Frame/mechanical RAD/OCT-CHBRA-AC.FCStd
Design/Electronic/Power/Resources/3dModels/Weidmuller-PM-5.08⁄90.stp
Design/Mechanical/CAD/Frame/Old Assemblies/furnace assembly.FCStd
Design/Mechanical/CAD/Frame/mechanical COTS/OCT-LDHNG-AA.FCStd
Design/Mechanical/CAD/Frame/mechanical COTS/Old Components/OCT-LFOOT-AA.FCStd
Design/Mechanical/CAD/Frame/mechanical COTS/Old Components/Protex 95-637SS spring loaded handle.FCStd
Design/Mechanical/CAD/Frame/mechanical COTS/Old Components/WAMF040.FCStd
Design/Mechanical/CAD/Frame/mechanical COTS/Old Components/WDS 8506-253-TO Handle.FCStd
Design/Mechanical/CAD/Frame/mechanical COTS/Old Components/WDS 8520-251 Handle.FCStd
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

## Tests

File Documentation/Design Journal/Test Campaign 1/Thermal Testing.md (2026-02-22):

Proposed tests, reasoning, desired results, measurements to take, etc.

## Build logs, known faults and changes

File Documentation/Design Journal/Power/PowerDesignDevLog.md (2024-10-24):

# Dev Log

## 04/09/23

My initial thought for providing power to the heating element in a controllable measurable way is through the use of a MOSFET driven with a PWM signal.
Next is to identify a suitable MOSFET with the following requirements.

- Low power losses and thus a temperate delta of at most +55°C. $I^2⋅R_{DS(on),max}⋅R_{thJA}<55$
- Can handle high enough power. $V_{DS}⋅I > K⋅P_{loss,max}$
- Low gate charge such that the operating frequency is above human hearing (20KHz) when driven by the low current output from a microcontroller.

where; $I$ is current flow through the MOSFET's drain, $R_{DS(on),max}$ is the maximum resistance of the MOSFET, $R_{thJA}$ is the increase in temperature of the MOSFET for a given power loss, $V_{DS}$ is the breakdown voltage between drain and source, K is some constant greater than 1, and $P_{loss,max}$ is the power maximum power loss through the walls of the furnace.

### IPP016N06NF2S

The [IPP016N06NF2S](https://www.mouser.co.uk/ProductDetail/Infineon-Technologies/IPP016N06NF2SAKMA1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) power MOSFET drew my eye as being relatively cheap (at £2.00 for a single unit), high enough max voltage and current, and low enough resistance. Looking at the [datasheet](https://www.mouser.co.uk/datasheet/2/196/Infineon_IPP016N06NF2S_DataSheet_v02_01_EN-3164870.pdf) for the IPP016N06NF2S i can establish whether this component meets the requirements.

- $R_{DS(on),max} =$ 1.6mΩ
- $R_{thJA} =$ 40°C/W
  Device on 40 mm x 40 mm x 1.5 mm epoxy PCB FR4 with 6 cm2 (one layer, 70 μm thick) copper area for drain.
  This is worst case, as we could just add a aluminium heatsink and a fan.
- $V_{DS} =$ 60v
- $I_D=$ 194A
- $Q_G=$ 155nC
  Where $I_D$ is the max drain current, and $Q_G$ is the charge required to fill the gate.

#### Power Losses And Max Current

Let calculate the maximum current as limited by a maximum delta temperature of the MOSFET of +55°C.

${I}^2⋅R_{DS(on),max}⋅R_{thJA}<55$

Filling in the values for $R_{DS(on),max}$ and $R_{thJA}$, we can get a value for the current at which the MOSFET temperature will have a delta of +55°C.

$I = 29.3$

29.3A is below the rated max current of 194A which is also great. Current flowing through the MOSFET should not exceed this value. Assuming the worst happened (the fan died and the heatsink got gunked), the MOSFET should not overheat.

#### Max Power

Now lets plug some more values into the following equation.

$V_{DS}⋅I = P$

I'm gonna knock 10v off the max voltage.

$50⋅29.3=1465$

1465W seems a sufficient amount of power.

#### Max Frequency

This is mostly a nice to have as it would still function below 20KHz but it would be annoying. I'm assuming the microcontroller in question can supply 25mA at most. And i'm going to simplify the mathematics here to get a ball park.

I need to calculate how long it takes for a given current to charge up the gate. The datasheet provides the charge and i've just assumed a current so here goes.

$t=Q/I$

$t=6.2⋅10^{-6}$s

which means...

$f = 1.61⋅10^5$Hz

~~That's significantly greater than 20KHz so i'm happy.~~

##### EDIT

I'm not happy. I forget this time $t$ is just the time it takes to charge up the gate. The switching time is equal to the time it takes to charge up and charge down the gate. So the time is actually doubled, the frequency is actually halved and the simplification i made earlier means the frequency is even lower. This means even if a microcontroller could drive the MOSFET it would be spending most of its time in periods of switching (is this even the correct wording?) where the voltage on the gate is somewhere between 0v and 12v. The resistance at these voltages is greater than it is at 12v and so the power losses would be higher. So i'm gonna say my next step is to investigate MOSFET drivers.

#### Conclusion

A max current of 29.3A, a max power of 1465W given that max current, ~~and a max frequency of 161KHZ~~ makes this MOSFET suitable when paired with a MOSFET driver. All for the low low price of 2.

## 06/09/23

I've been toying around with [this paper](https://sci-hub.st/10.1080/00207217.2019.1625973) in [Falstad CircuitJS](http://falstad.com/circuit/circuitjs.html). You can find the file for the circuit i made [here](obsidian://open?vault=furnace-mk2&file=Power%20Design%2FResources%2FMOSFET_OCP). To open it just copy the text from within the file to the "import from text" option under File in CircuitJS. It works somewhat but trying to get it to shutoff at exactly 29.3A is difficult. I think experimentation should continue in a more robust simulation software - one that comes to mind is the real world.

## 09/09/23

I have devised a way for the shut off current to be much more precise. The circuit described in the paper relies on the voltage drop across the diode to be a specific value V<sub>D</sub>. This value is dependent on the current across said diode. A current which changes when adjustments are made to voltage divider and when the base of the transistor starts conducting. However by separating the diode and the transistors base with an opamp set up as a comparator there will be very minimal change in current across the diode. With the voltage V<sub>F</sub> being measured by the opamp's negative terminal and a reference voltage V<sub>ref</sub> being measured by the opamp's positive terminal, the exact moment the current i<sub>d</sub> is sufficiently high to cause V<sub>F</sub> to increase above V<sub>ref</sub> can be detected and capacitor C<sub>d</sub> will begin to be charged by the opamps 12v output.

I have modified my CircuitJS circuit to demonstrate this [here](obsidian://open?vault=furnace-mk2&file=Power%20Design%2FResources%2FMOSFET_OCP_V2). The scopes along the bottom of the screen are used to track some specific values. Namely the voltages across C<sub>d</sub> (in red) and C<sub>t</sub> (in green), current across the current across the MOSFET and heating element (in yellow), and the voltages V<sub>F</sub> (in red) and V<sub>ref</sub>.

### Using the CircuitJS demonstration

It might not be so intuitive how exactly to use this circuit within CircuitJS so here's a quick guide.

1. Wait for the voltage, V<sub>b</sub>, across C<sub>t</sub>, represented by the green line on scope 1, to increase to 2v. Current, i<sub>d</sub>, should begin to flow through the MOSFET, represented by the yellow line in scope 2.
2. You should notice that V<sub>F</sub> should have changed to a value closer to V<sub>ref</sub>, represented by the red and green lines in scope 3. By increasing the value of the slider labelled "Load" on the right side of the screen you will decrease i<sub>d</sub> and V<sub>F</sub>.
3. By decreasing the value of load slowly you will increase i<sub>d</sub> and V<sub>F</sub>. The moment V<sub>F</sub> is greater than V<sub>ref</sub>, V<sub>b</sub> should increase rapidly causing the transistor to dump the charge stored by C<sub>t</sub> and subsequently turn the MOSFET off.

## 18/10/24

### Version 3

After the 1st and 2nd iterations were found to have their flaws i've decided to come back to you and talk through the design process to avoid any more errors. First of all the components. The MOSFET has been decided upon above. All that's left is: The MOSFET driver, the OpAmps, the NPN tranistor, the diode, and the various resistors and capacitors. For whatever reason, for v1 and v2, I decided that this board must be accomplished using surface mount components despite for the low number of components on a relatively large board. To makes for easier manufactoring and reproducability going back to basics and using through hole components is an all around better desision.

Along with this version is an updated circuitJS design MOSFET_OCT_V3

#### MOSFET - IPP016N06NF2SAKMA1

<https://uk.rs-online.com/web/p/mosfets/2601208P?gb=s>

#### MOSFET Driver - UCC27524P

<https://uk.rs-online.com/web/p/gate-drivers/8124303P>

#### OpAmp - LM258AP

<https://uk.rs-online.com/web/p/op-amps/6610502>
The LM258 is rated for sligthly higher temps than the more standard LM358 which I thought would be more fitting for use in a furnace. But a 358 could be used here probably just fine.

#### NPN Transistor - PN2222ATA

<https://uk.rs-online.com/web/p/bipolar-transistors/7390381>
The OpAmp driving the transistors base has a 4.7k resistor limiting current to 2.6mA. The transistor has to be able to handle 2.6 \* h<sub>fe</sub> mA of current. With a max h<sub>fe</sub> of 300 and a max current of 1A, the PN2222 is able to handle that.

#### Diode - 1N4004

<https://uk.rs-online.com/web/p/schottky-diodes-rectifiers/6289029?gb=s>
The 1N4004 is definetly overkill but it's what the simulation used.

#### Resistors and Capacitors

With the majority of the resistors in use on the circuit being used for measurements I've decided the error should be no more than 1%.

#### Potentiometer - 3296W

<https://uk.rs-online.com/web/p/trimmer-potentiometers/5219647>

#### Screw Terminal - Weidmuller PM 5.08/90

<https://uk.rs-online.com/web/p/pcb-terminal-blocks/4258720>

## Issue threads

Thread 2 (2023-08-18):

perform thermal analysis of walls and heating element

DeltaFwulf, 2023-08-18:
calculate wire temperatures and chamber wall power losses at design temperatures

Outputs:
> heating element dT at design temperature
> graphs of results
     - wall thickness vs power
     - wire area vs dT
     - furnace power loss vs chamber temperature
     - wire [area, power, temperature] assuming a cold chamber (STP) to calculate max wire power

Stellaramie, 2023-10-08:
--- Conservative estimate ---
Chamber dimensions: 76mm of brick, 200mm of rock wool
Required power: 112W @ 1100C

Closed 2023-10-08.

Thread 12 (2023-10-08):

Prototype metal cutting and bending

Stellaramie, 2023-10-08:
Is it possible to cut and bend the sheet metal ourselves?

DeltaFwulf, 2024-10-20:
the cutting can be accomplished at Cardiff Hackspace using a CNC mill.

DeltaFwulf, 2025-04-20:
tools have been selected for manufacture of the frame, and laser cut parts are being manufactured as of comment writing.

Closed 2025-04-20.

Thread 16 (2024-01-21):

optimise frame for manufacture

DeltaFwulf, 2024-01-21:
optimise furnace frame for lower cost manufacture, integrate sump to catch spilled metal.

DeltaFwulf, 2024-10-20:
The sump has been cut out in favour of moving spill paths to avoid critical components. Also, the furnace assembly is to be redrawn using native assembly functionality for ease of maintenance going forwards.

DeltaFwulf, 2024-11-24:
The cost of manufacture has been reduced by duplicating components where possible, reducing stock thicknesses, and using machines available to us instead of outsourcing.

Closed 2024-11-24.

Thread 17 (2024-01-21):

Power Delivery v2

Stellaramie, 2024-01-21:
**Updates required for v2**

- PS-EN pin needs to not be left floating and prefferably driven by the ESP32
- Use a trace of know resistance for the current sense resistor
-

Stellaramie, 2024-10-17:
v2 created to the specifications listed on the issue and any issues identified with the v1 board.

Closed 2024-10-17.

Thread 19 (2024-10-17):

Power Delivery v3

Stellaramie, 2024-10-17:
**Description**
Upon completing v2 and sending for the PCBs i realised yet some more changes to be made to the board:
- Make use of through hole components for easier manufacturing.
- Use a screw terminal block that is easily sourced.
- Caps on the voltage supplies of the logic chips.
- Power on LEDs

**Tasks**
- Update dev-log with a list of components and why they were picked.
- Update and tidy up the schematic to include correct component names, datasheets, and footprints.

Stellaramie, 2024-11-24:
Board v3 created

Closed 2024-11-24.

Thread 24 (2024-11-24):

FreeCAD native assembly

DeltaFwulf, 2024-11-24:
FreeCAD has integrated a native assembly workbench. For ease of long-term maintenance and stability, the furnace assembly will be reintegrated using this workbench, instead of the previously used Assembly4 add-on. The file structure will also be changed and a more useful naming scheme adopted.

Several weaknesses in the original design will also be improved upon during the remodel, including the lid - chamber interface.

DeltaFwulf, 2025-04-20:
furnace is now fully modelled using native assembly workbench.

Closed 2025-04-20.

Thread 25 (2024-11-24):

Power Delivery v4

Stellaramie, 2024-11-24:
**Description:**
v3 of the power delivery board has these issues:
- The Molex connectors didn't have enough clearance on the side of the latch.
- The heat spreader for the MOSFET wasn't connected to the correct pin.
- The silkscreen symbol for the transistor was backwards to the way it actually went in.
- QR code is a little small.

**Solutions:**
- Move all other components over from the screw terminals.
- connect the heat spreader under the MOSFET up to pin 2 and provide enough area and vias for good heat dissipation.
- Use a more ambiguous symbol for the transistor so it doesn't confuse anyone assembling the board.
- Make the QR code bigger.

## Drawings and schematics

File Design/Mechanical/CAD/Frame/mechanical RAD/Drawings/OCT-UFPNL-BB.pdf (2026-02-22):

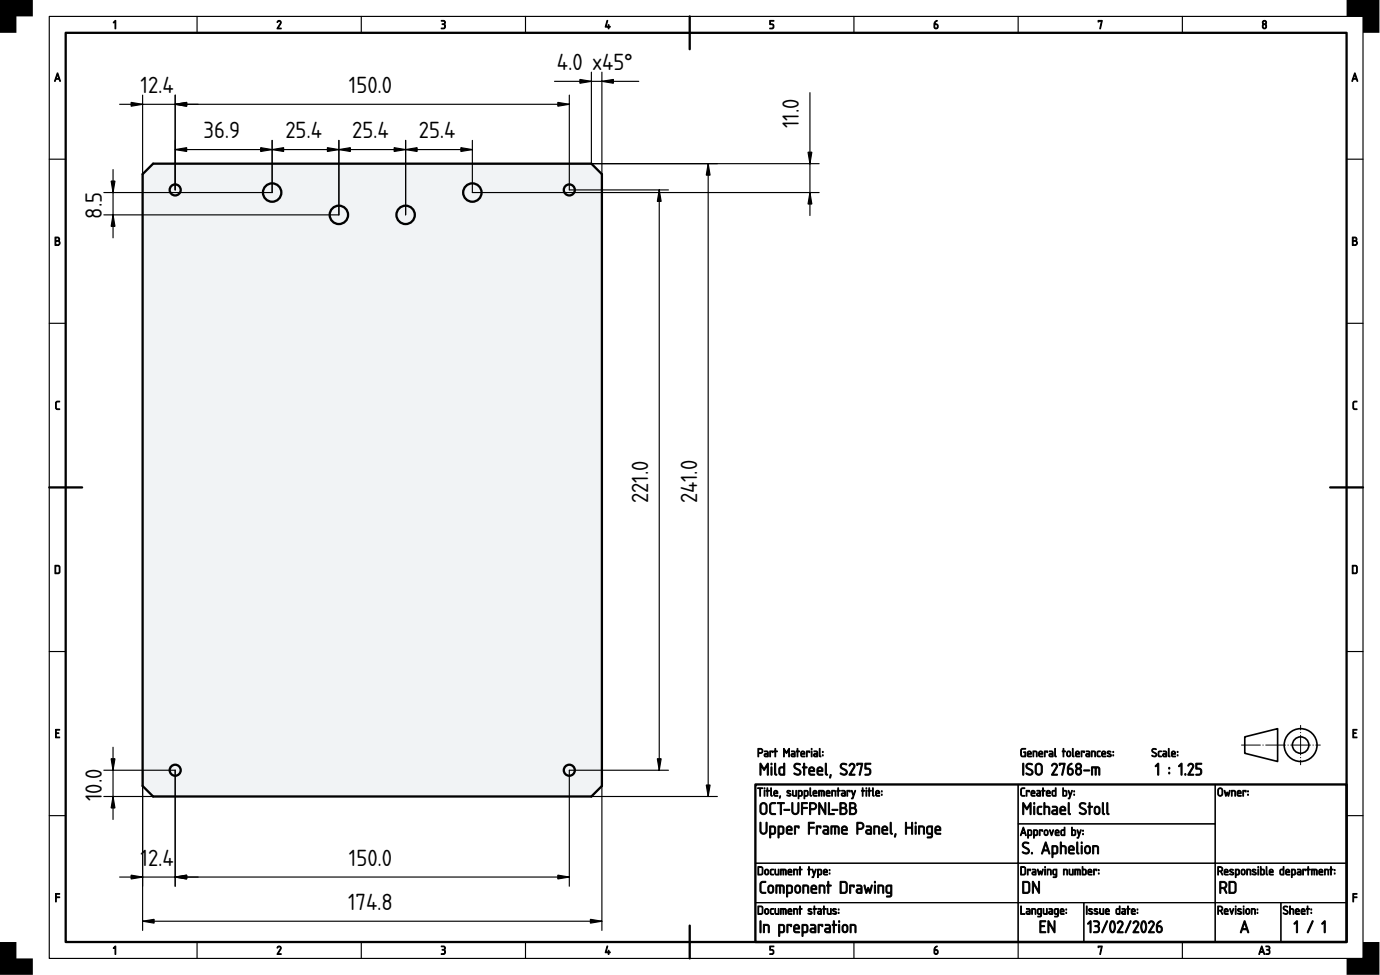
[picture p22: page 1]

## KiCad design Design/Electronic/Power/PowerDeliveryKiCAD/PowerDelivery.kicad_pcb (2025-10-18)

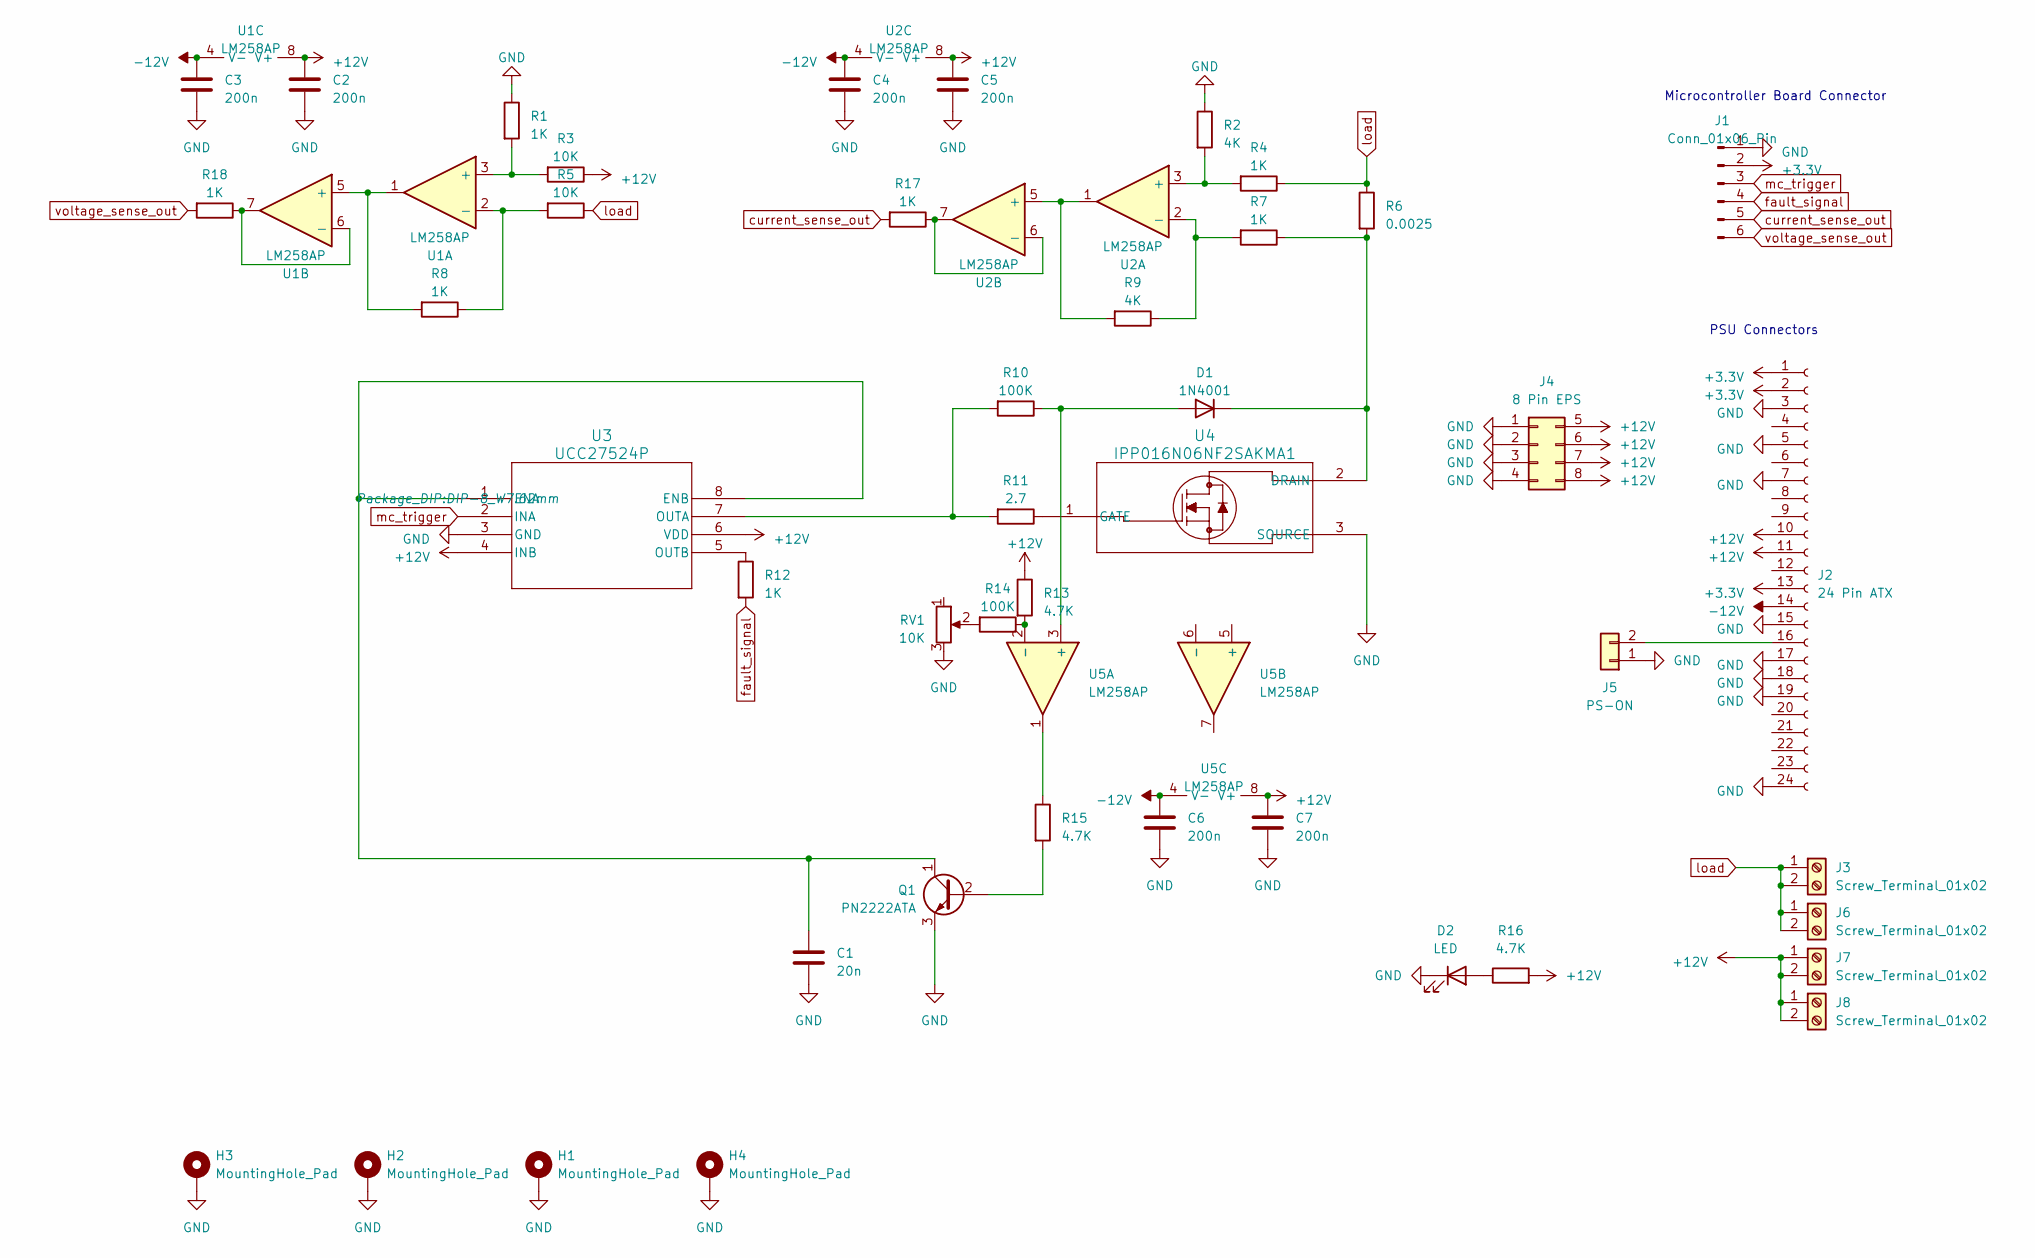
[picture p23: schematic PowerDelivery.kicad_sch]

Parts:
C1: 20n; C_Disc_D3.8mm_W2.6mm_P2.50mm
C2, C3, C4, C5, C6, C7: 200n; C_Disc_D3.8mm_W2.6mm_P2.50mm
D1: 1N4001; D_DO-41_SOD81_P7.62mm_Horizontal
D2: LED; LED_D5.0mm
H1, H2, H3, H4: MountingHole_Pad; MountingHole_3.2mm_M3_ISO7380_Pad
J1: Conn_01x06_Pin; PinHeader_1x06_P2.54mm_Vertical
J2: 24 Pin ATX; Molex_Mini-Fit_Jr_5566-24A_2x12_P4.20mm_Vertical
J3, J6, J7, J8: Screw_Terminal_01x02; TerminalBlock_bornier-2_P5.08mm
J4: 8 Pin EPS; Molex_Mini-Fit_Jr_5566-08A_2x04_P4.20mm_Vertical
J5: PS-ON; PinHeader_1x02_P2.54mm_Vertical
Q1: PN2222ATA; TO-92_Wide
R1, R4, R7, R8, R12, R17, R18: 1K; R_Axial_DIN0207_L6.3mm_D2.5mm_P7.62mm_Horizontal
R2, R9: 4K; R_Axial_DIN0207_L6.3mm_D2.5mm_P7.62mm_Horizontal
R3, R5: 10K; R_Axial_DIN0207_L6.3mm_D2.5mm_P7.62mm_Horizontal
R6: 0.0025; R_Axial_DIN0617_L17.0mm_D6.0mm_P20.32mm_Horizontal
R10, R14: 100K; R_Axial_DIN0207_L6.3mm_D2.5mm_P7.62mm_Horizontal
R11: 2.7; R_Axial_DIN0207_L6.3mm_D2.5mm_P7.62mm_Horizontal
R13, R15, R16: 4.7K; R_Axial_DIN0207_L6.3mm_D2.5mm_P7.62mm_Horizontal
RV1: 10K; Potentiometer_Bourns_3296W_Vertical
U1, U2, U5: LM258AP; DIP-8_W7.62mm
U3: UCC27524P; DIP-8_W7.62mm
U4: IPP016N06NF2SAKMA1; TO-220-3_Horizontal_TabDown

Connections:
+3.3V: J1.2, J2.1, J2.2, J2.13
+12V: C2.1, C5.1, C7.1, J2.10, J2.11, J4.5, J4.6, J4.7, J4.8, J7.1, J7.2, J8.1, J8.2, R3.1, R13.1, R16.2, U1.8 (V+), U2.8 (V+), U3.4 (INB), U3.6 (VDD), U5.8 (V+)
-12V: C3.1, C4.1, C6.1, J2.14, U1.4 (V-), U2.4 (V-), U5.4 (V-)
GND: C1.2, C2.2, C3.2, C4.2, C5.2, C6.2, C7.2, D2.1 (K), H1.1, H2.1, H3.1, H4.1, J1.1, J2.3, J2.5, J2.7, J2.15, J2.17, J2.18, J2.19, J2.24, J4.1, J4.2, J4.3, J4.4, J5.1, Q1.3 (E), R1.1, R2.1, RV1.3, U3.3 (GND), U4.3 (SOURCE)
unnamed: D1.2 (A), R10.1, U5.3 (+)
unnamed: D1.1 (K), R6.2, R7.1, U4.2 (DRAIN)
unnamed: D2.2 (A), R16.1
unnamed: J2.16, J5.2
unnamed: Q1.2 (B), R15.2
unnamed: C1.1, Q1.1 (C), U3.1 (ENA), U3.8 (ENB)
unnamed: R14.2, RV1.2
unnamed: R15.1, U5.1
unnamed: R1.2, R3.2, U1.3 (+)
unnamed: R5.2, R8.1, U1.2 (-)
unnamed: R8.2, U1.1, U1.5 (+)
unnamed: R18.1, U1.6 (-), U1.7
unnamed: R2.2, R4.2, U2.3 (+)
unnamed: R7.2, R9.1, U2.2 (-)
unnamed: R9.2, U2.1, U2.5 (+)
unnamed: R17.1, U2.6 (-), U2.7
unnamed: R10.2, R11.2, U3.7 (OUTA)
unnamed: R12.1, U3.5 (OUTB)
unnamed: R11.1, U4.1 (GATE)
unnamed: R13.2, R14.1, U5.2 (-)
current_sense_out: J1.5, R17.2
fault_signal: J1.4, R12.2
load: J3.1, J3.2, J6.1, J6.2, R4.1, R5.1, R6.1
mc_trigger: J1.3, U3.2 (INA)
voltage_sense_out: J1.6, R18.2

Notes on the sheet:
PSU Connectors
Microcontroller Board Connector

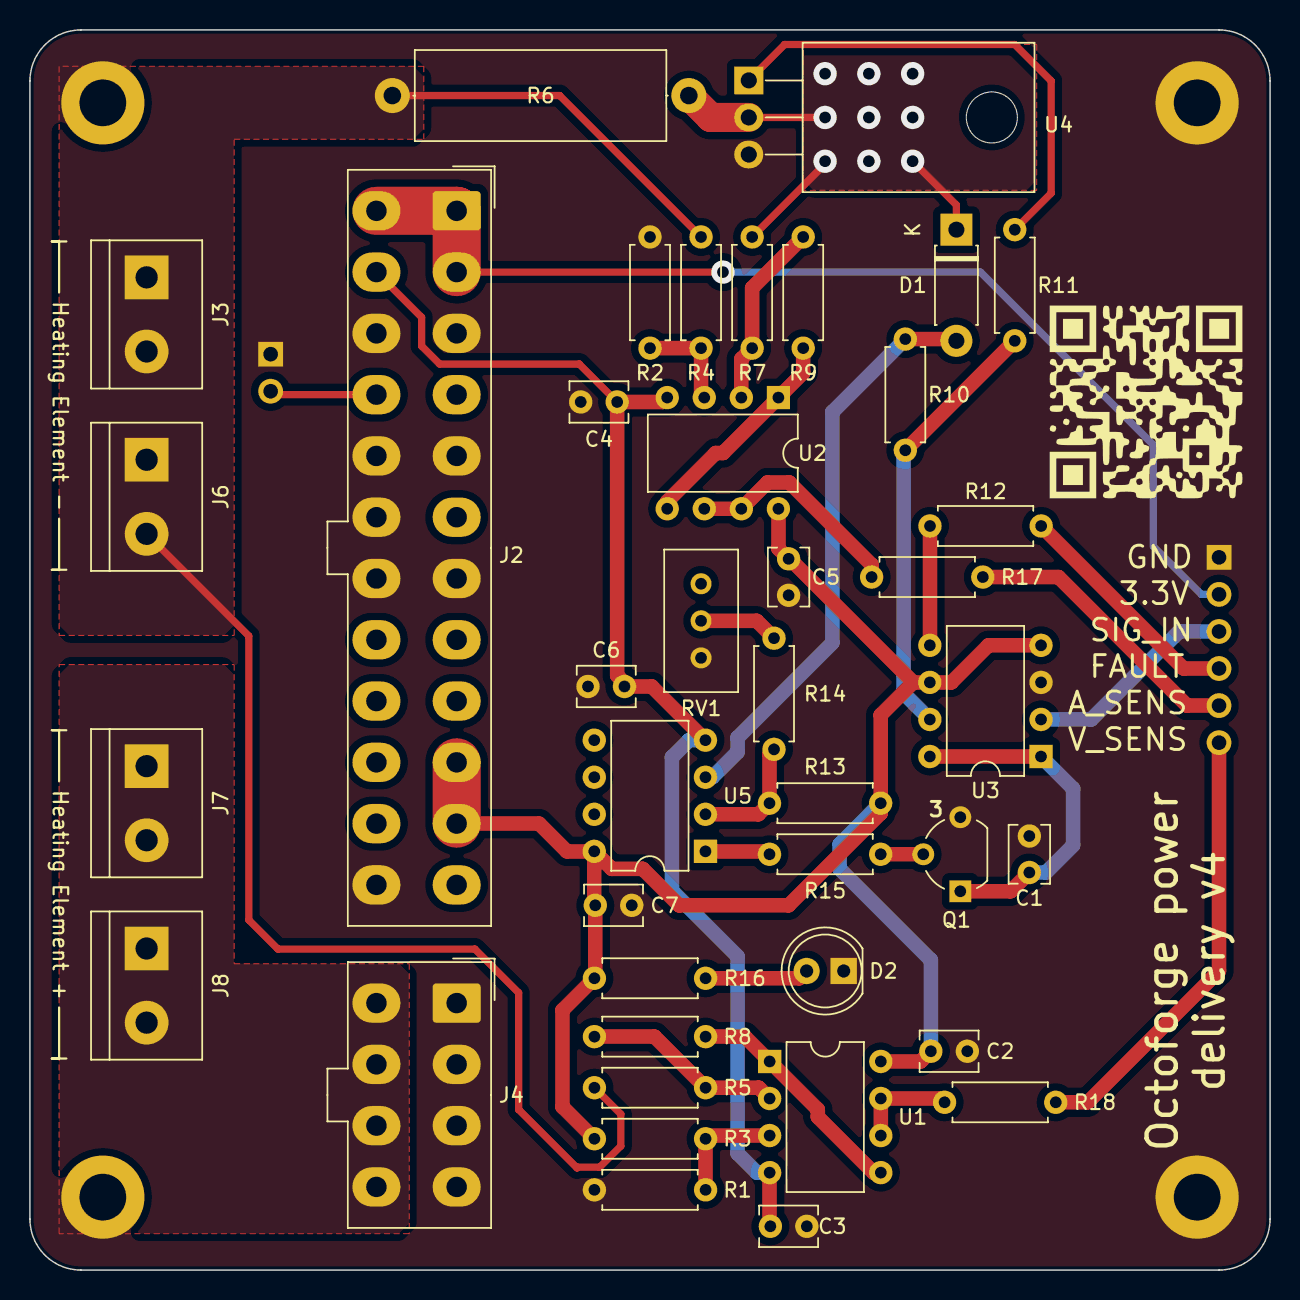
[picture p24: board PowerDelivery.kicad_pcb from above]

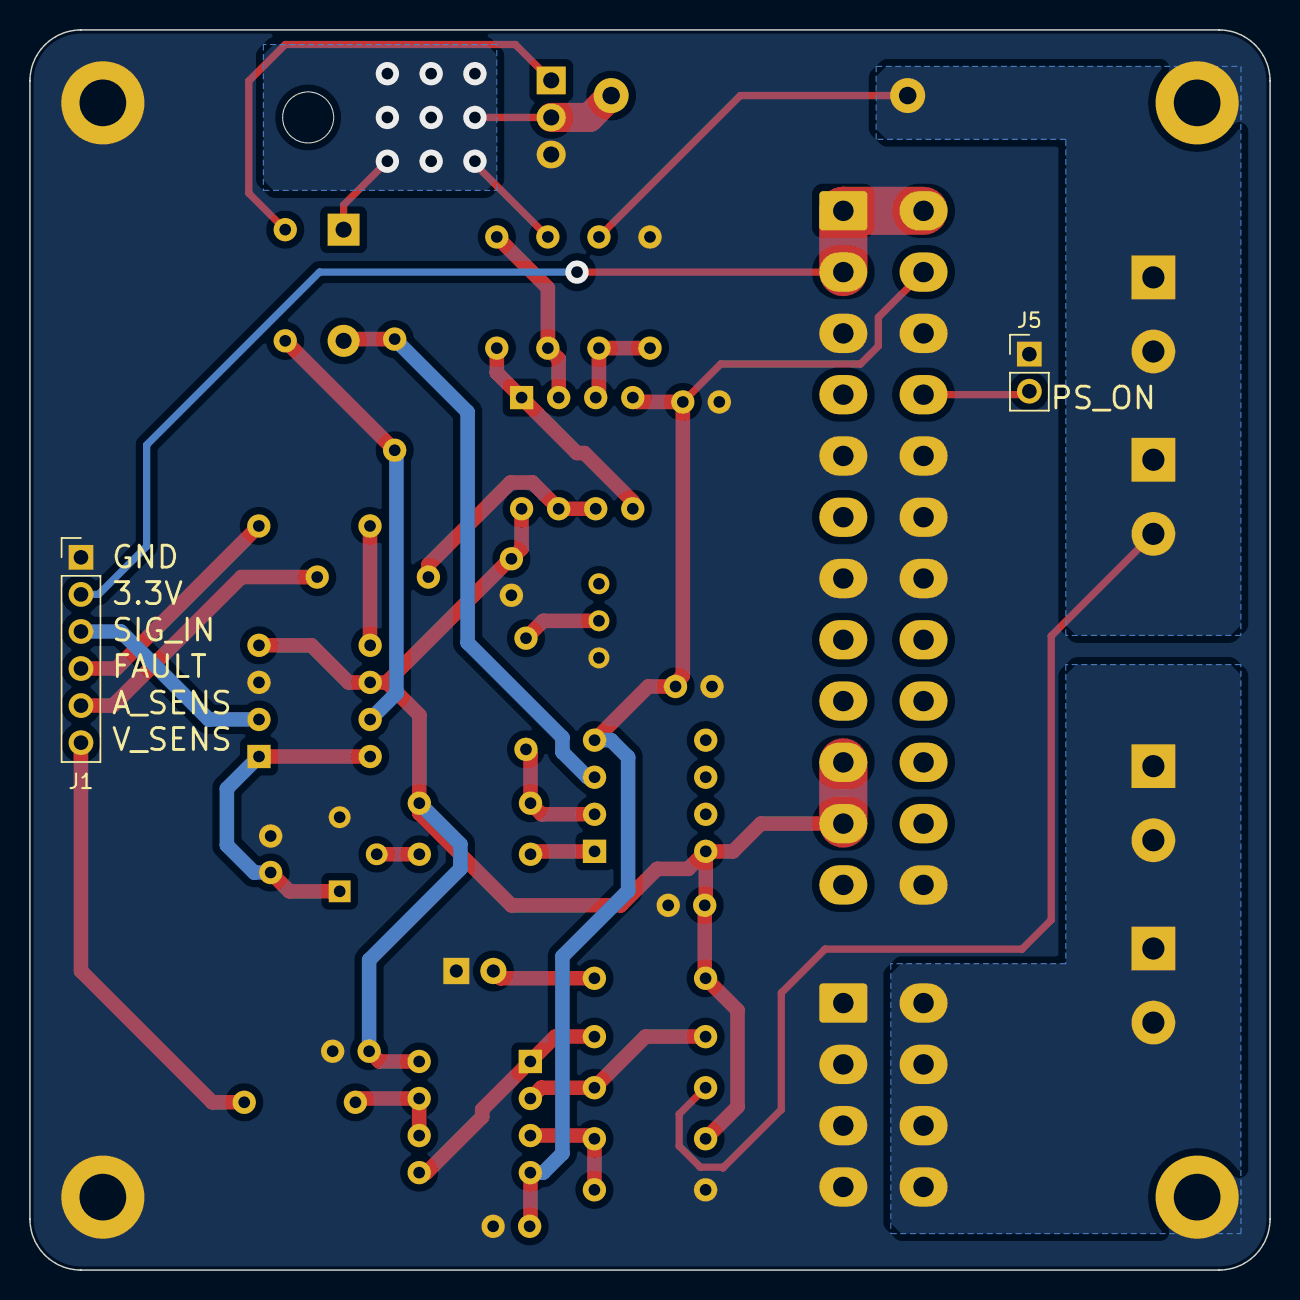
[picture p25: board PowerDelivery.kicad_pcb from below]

Board: 2 copper layers, 85.0 x 85.0 mm, 46 parts (2 on the bottom side), 29 nets.

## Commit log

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2023-08-20 implemented design point solver
    I have implemented a convoluted solver to get key furnace performance data at a single chamber temperature and power. It's currently having weird complex number issues but this will hopefully not be too bad to iron out
2023-09-03 inner wall fixed as chamber temperature
    Modelled the furnace as having its inner wall surface temperature equal to the chamber temperature in an attempt to fix suspected underprediction of heat loss
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2023-10-06 added heating elements
    working out how to create larger assemblies in FreeCAD
    [000_000 furnace.FCStd, 100_000 assembly.FCStd, 100_001 wall brick.FCStd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]
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2023-10-09 exoskeleton begins
    modelled casing base and side panels
    [300_000 frame assembly.FCStd, 300_001 exoskeleton base.FCStd, 300_002 side panel.FCStd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]
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2024-01-01 moved connectors and added mounting holes
    [PowerDelivery.kicad_pcb]
2024-01-02 designed furnace frame
    An initial furnace frame has been designed and modelled in freeCAD. Insulation has been partially modelled.
    [000_000 furnace.FCStd, 100_001 wall brick.FCStd, 100_002 front brick.FCStd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]
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2024-01-21 lid tweaks
    lid made more cheaperer
    [000_000 furnace.FCStd, 100_001 wall brick.FCStd, 100_002 front brick.FCStd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]
2024-02-02 replaced hinge
    updated hinge to match final component
    [000_000 furnace.FCStd, 100_101 lid insulation.FCStd, 300_000 frame assembly.FCStd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]
2024-02-07 updated front panel
    changed front panel cut-out to individual components, modelled PCB cooling duct, added BOM to mechanical design.
    [000_000 furnace.FCStd, 100_001 wall brick.FCStd, 100_002 front brick.FCStd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]
2024-02-15 updated chamber bricks
    - element holes split over two bricks
    - thermocouple hole included
    [000_000 furnace.FCStd, 100_000 chamber.FCStd, 100_001 wall brick.FCStd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]
2024-04-14 refactored thermal model
    added temperature distribution plotter and renamed symbols for easier reading.
    [200_006 terminal block.FCStd, 300_000 frame assembly.FCStd, 300_001.step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]
2024-10-12 Create power delivery V2
    [PowerDelivery.kicad_pcb, PowerDelivery.kicad_sch]
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2024-10-19 began revision 2 assembly
    began drawing a native assembly based version of Octoforge in FreeCAD
    [000_000 furnace.FCStd, 100_004 base insulation.FCStd, 100_101 lid insulation.FCStd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]
2024-10-19 continued frame design
    most of the frame has been remodelled.
    [000_000 furnace.FCStd, 100_004 base insulation.FCStd, 300_000 frame assembly.FCStd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]
2024-10-23 Remaining files to be commited
    [Molex-Mini-Fit-Jr-5566-24.stp, Molex-Mini-Fit-Jr-5566-8.stp, PowerDelivery.kicad_pcb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]
2024-10-24 lower frame redrawn
    the lower frame and panels have been included in the rev2 assembly. BOM updated
    [000_000 furnace.FCStd, 100_000 chamber.FCStd, 100_002 front brick.FCStd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]
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2024-12-03 reworked assembly up to lid section
    native assembly has been remade with fixed constrains up to the chamber bricks and frame main body.
    [BOM.ods, Frame assembly.FCStd, OCT-CHBAS-AA.FCStd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]
2024-12-14 began lid model
    the lid has been redesigned for better thermal performance. Modelling has begun with the brick and frame profile modelled so far.
    [300_013 lid hinge v2.FCStd, BOM.ods, OCT-CHBAS-AA.FCStd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]
2024-12-20 frame redesign completed
    The majority of the redesign has been completed, the only major details remaining are the electrical components and handles.
    [BOM.ods, OCT-CHBAS-AA.FCStd, OCT-CHBRK-AA.FCStd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]
2024-12-29 power terminals
    The power terminals have been included in the assembly, as well as handle holes for carry handles.
    [BOM.ods, OCT-CHBAS-AA.FCStd, OCT-CHBRK-AA.FCStd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]
2025-04-20 furnace assembly B
    Due to cost constraints, the furnace was revisioned to B, with a redesigned lower section for lower cost, compactness, and ease of assembly.
    [BOM.ods, OCT-ATXPS-AA.FCStd, OCT-CHAND-AA.FCStd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]
2025-10-18 Made changes from v3
    [PowerDelivery-B_Cu.gbl, PowerDelivery-B_Mask.gbs, PowerDelivery-B_Paste.gbp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]
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2026-02-06 updated brackets
    Changed cut to 45 degree on brackets for ease of manufacture.
    [OCT-LBRAC-AA.FCStd, OCT-LFPNL-AB.FCStd, OCT-UBRAC-AA.FCStd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]
2026-02-07 updated frame bracket design
    Changed holes to 4.2 mm, added part drawings.
    [OCT-ATXPS-AA.FCStd, OCT-CHBAS-AA.FCStd, OCT-CHBRA-AA - no holes.step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]
2026-02-07 Tidy up file structure
    [000_000 furnace.FCStd, 100_000 chamber.FCStd, 100_002 front brick.FCStd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]
2026-02-09 reworked lower blocks, upper panels
    Added block brackets for lower panels, upper panels, and upper panel brackets.
    [OCT-ATXPS-AA.FCStd, OCT-CFPNL-AA.FCStd, OCT-CHBAS-AA.FCStd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]
2026-02-14 updated frame components
    remodelled panel blocks, upper panels, upper panel brackets.
    [OCT-ATXPS-AA.FCStd, OCT-CFPNL-AA.FCStd, OCT-CHBAS-AA.FCStd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]
2026-02-15 added frame fasteners
    Included fasteners holding frame together and lifting handle fasteners.
    [BOM.ods, OCT-ATXPS-AA.FCStd, OCT-CHBAS-AA.FCStd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]
2026-02-16 added final fasteners to the frame
    Fasteners have been added to the lid hinge.
    [OctoForge.FCStd]
2026-02-16 added lid handle
    Sourced a lid handle, included in GA and added associated fasteners.
    [OCT-ATXPS-AA.FCStd, OCT-CHBAS-AA.FCStd, OCT-CHBRK-AA.FCStd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]
2026-02-20 began work on BOM
    Renamed assembly components and reworked lid hinge fasteners for better visibility in BOM
    [BOM.ods, OctoForge.FCStd, bom_export.csv]
2026-02-22 rebuilt fastener parts to appear on fastener BOM
    The BOM tools provided by FreeCAD's Assembly and Fastener WBs will now populate with all components, with reasonable part names. Added an explanation as to how this was done in design journal.
    [BOM intermediate.ods, BOM.ods, OCT-ATXPS-AA.FCStd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]
2026-02-22 added BOM
    The BOM now contains up to date information about the frame components, as of 22/02/2026.
    [BOM intermediate.ods, BOM old.ods, BOM.ods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]
2026-02-22 updated OCT-LFPNL-CA design to complete
    ATX PSU panel OCT-LFPNL-CA was corrected against known good mounting pattern. BOM updated with stock / buy information.
    [BOM.ods, OCT-CHBRA-AB.FCStd, OCT-CHBRA-AB.step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]
2026-02-22 Replaced old COTS components
    Updated COTS component CAD and BOM entries where better alternatives were found. The front lower panel (OCT-LFPNL-BA) has been marked as design complete.
    [BOM.ods, OCT-CHAND-AA.FCStd, OCT-FRAME-A.FCStd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]
2026-03-04 began heating element sizing calculations
    [BOM.ods, OCT-ATXPS-AA.FCStd, OCT-CHAND-AA.FCStd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]
2026-03-05 preliminary element geometry
    The heating element geometry has a preliminary solution and basic CAD model. The furnace chamber bricks have also been remodelled within a single file named OCT-CHMBR-A
    [OCT-CHBAS-AA.FCStd, OCT-CHBRK-AA.FCStd, OCT-CHBRK-BA.FCStd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]
2026-03-07 heating element modelled
    OCT-HWIRE-AA has been modelled using some FreeCAD dark magic.
    [OCT-HELEM-AA.FCStd, OCT-HWIRE-AA.FCStd]
2026-03-08 heating elements included in GA (#48)
    The GA model now has the heating elements included.
    [BOM.ods, OCT-CHBRA-AC.FCStd, OCT-CHMBR-A.FCStd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]
2026-03-08 updated BOM
    Corrected heating element file name to OCT-HELEM-A, updated Bill of Materials to current status.
    [BOM.ods, Coil Winder.FCStd, OCT-HELEM-A.FCStd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]
2026-03-10 Improved heating element render performance
    The angular deflection has been relaxed from 6.4 degrees to 15 degrees, reducing rendering overhead and reducing recompute times.
    [OCT-HELEM-A.FCStd, OctoForge-A.FCStd]
